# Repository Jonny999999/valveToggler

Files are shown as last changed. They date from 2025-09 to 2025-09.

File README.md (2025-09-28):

# ValveToggler-24V (Pneumatic Dust Filter Shaker)
Small analog controller PCB that drives a **5/3 pneumatic valve (2 coils)** to shake dust filters of a wood-chip extraction system (*Holzspäne-Absaugung*).  

<p align="center">
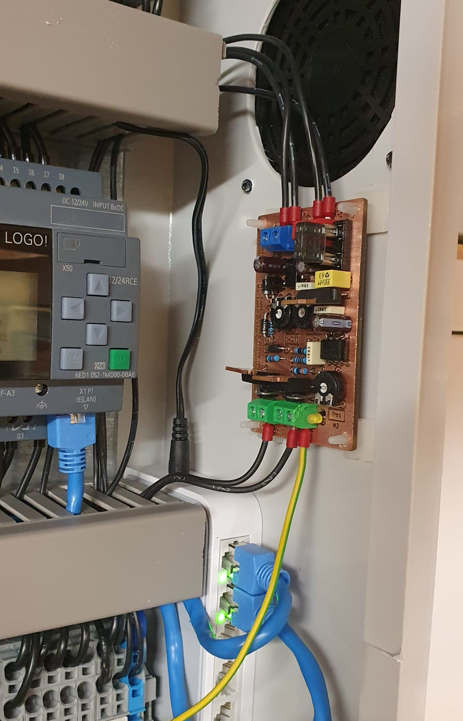
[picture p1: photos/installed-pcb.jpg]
Installed PCB – ValveToggler-24V
  
</p>

*Motivation:* Take switching stress off a LOGO! PLC's **relay outputs** (high-frequency switching, inductive load, continuous use over years) by moving the coil drive to **MOSFETs** and hardware timers. The PLC now only provides **high-impedance continuous signals** to enable/disable the shaking in the desired mode.

---

## System Hardware
- **24 V DC** supply (same rail as valve coils)
- **5/3-way pneumatic valve** with two **24 V** coils
- **Double acting pneumatic cylinder** shaking the filters
- **Mechanical stops** at cylinder's limits for abrupt stop so the dust falls off
- Two PLC control lines: `MODE_SINGLE_24V`, `MODE_DOUBLE_24V` (double has priority)

## PCB Features
- Steps **24 V** mode lines to **12 V**, generates timing with 2x **NE555**
- **Modes & timing**  
  - **SINGLE:** Toggle Coil1 only, with independent **ON/OFF** time (typ. ~300 ms ON, ~1.0 s OFF)  
     Adjustable range ≈ **70 – 400 ms** / **0.1 – 3 s**
  - **DOUBLE:** **50 % duty**, **complementary** coil drive (COIL1 = ¬COIL2)  
     Half-period adjustable from **50 ms to 3 s**
- **Low-side N-MOSFET** drivers, flyback/TVS, indicator LEDs
- Input priority & interlock to prevent both coils ON

---

## Files
- **[Schematic (PDF)](export/ValveToggler_schematic.pdf)**
- **[Layout (PNG)](export/ValveToggler_layout.jpg)**

## Schematic + layout preview:  
<p align="center">
  <a href="export/ValveToggler_schematic.pdf">
    Schematic
  </a>
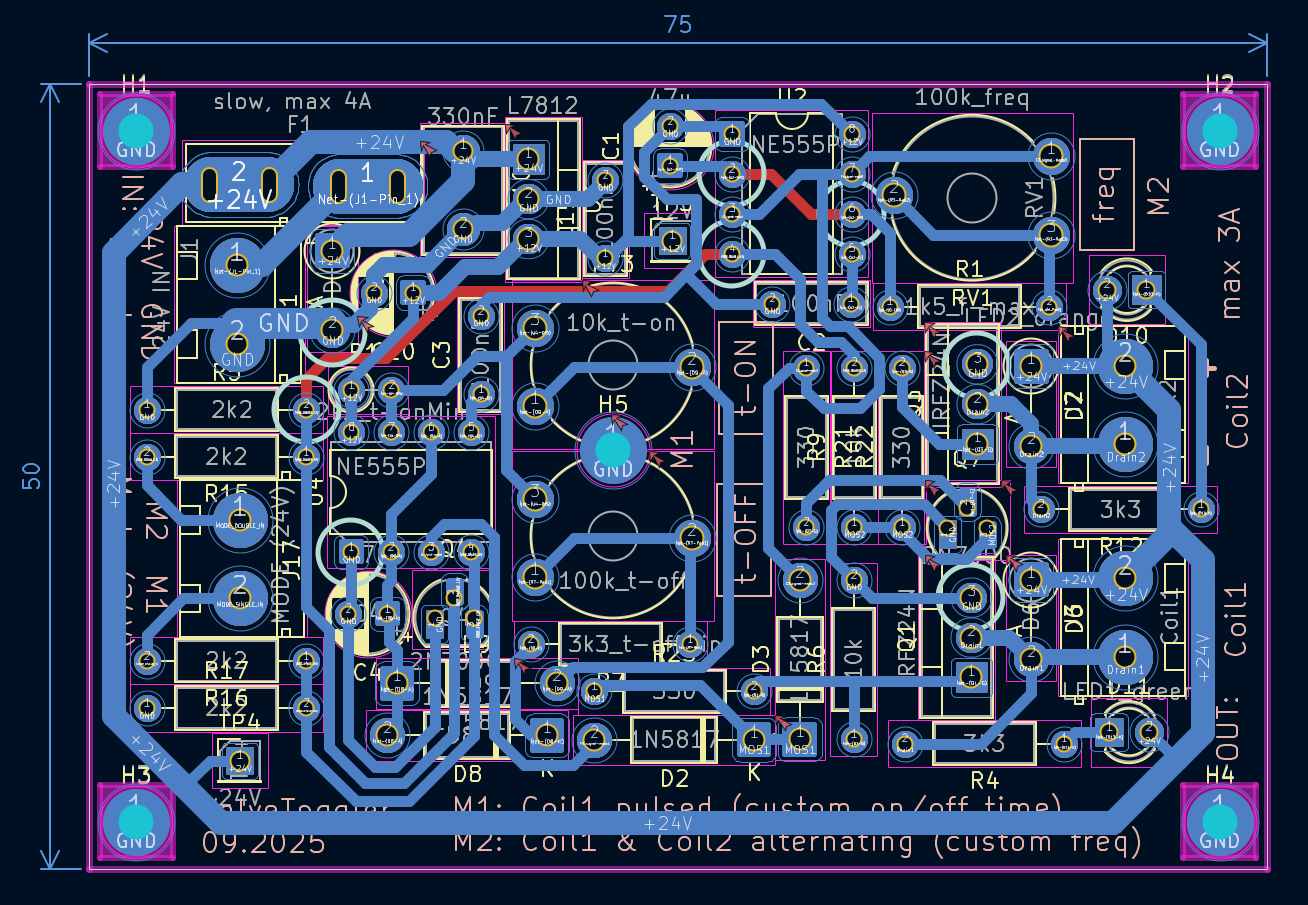
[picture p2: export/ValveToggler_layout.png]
PCB Layout
  
</p>

## Photos
Milling and Soldering:
<p align="center">
  <a>
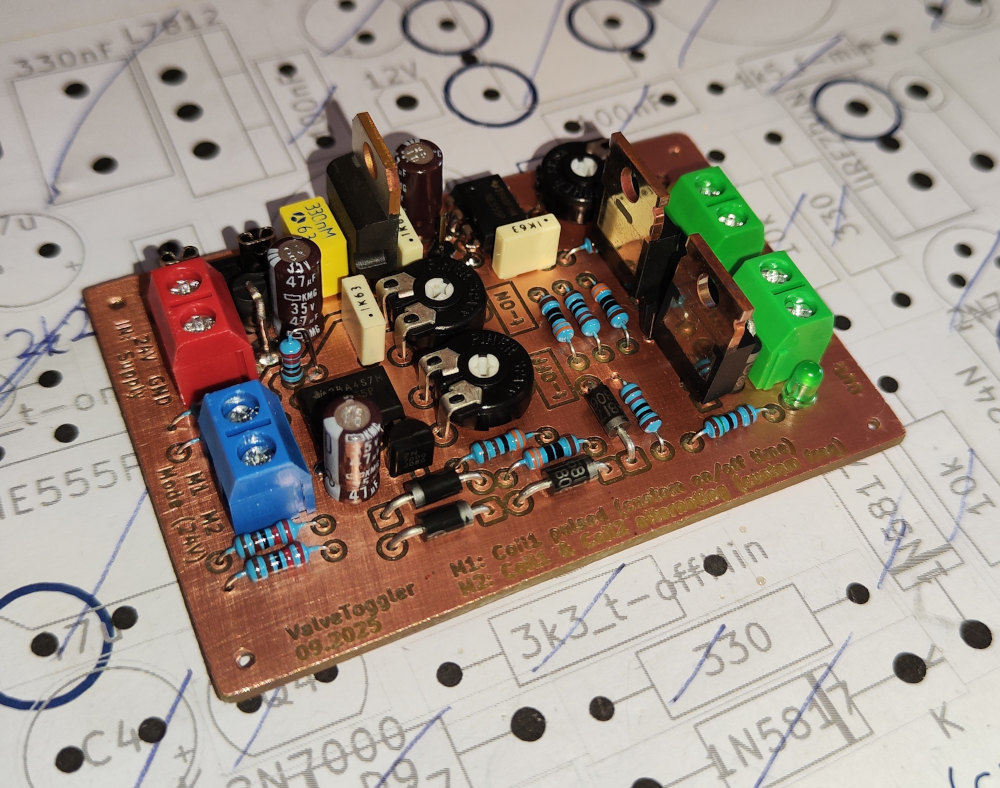
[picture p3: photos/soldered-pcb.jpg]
soldered pcb
    
  </a>
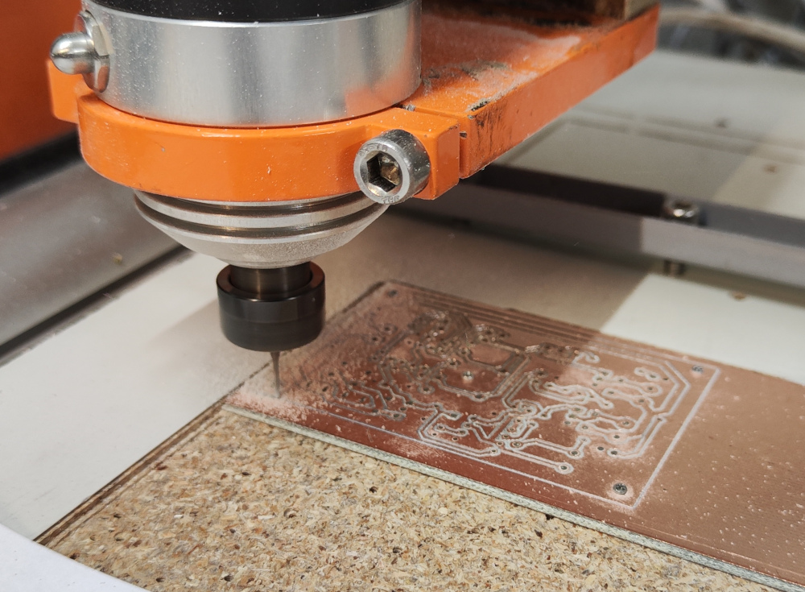
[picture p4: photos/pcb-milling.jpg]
pcb milling
    
</p>

<br>

3D-Model and Finished pcb:
<p align="center">
  <a>
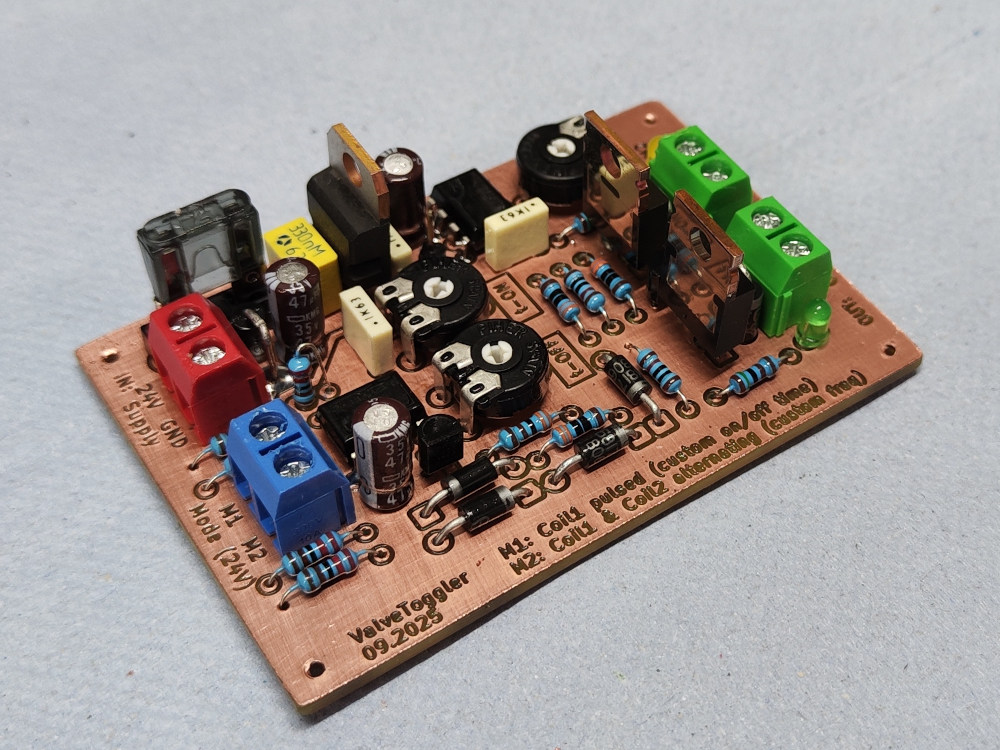
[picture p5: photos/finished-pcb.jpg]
    
  </a>
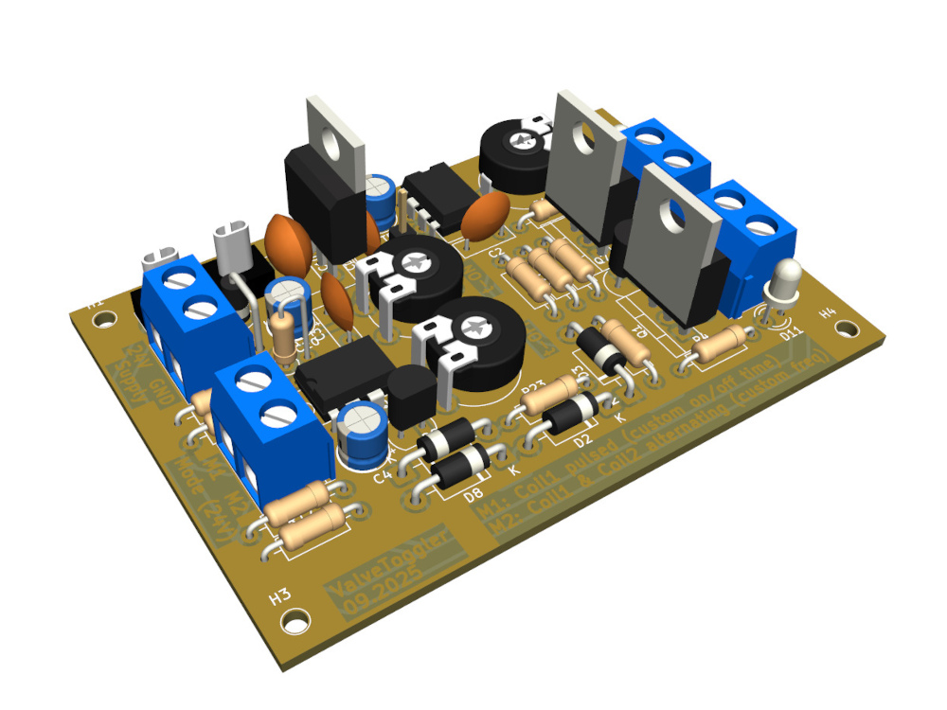
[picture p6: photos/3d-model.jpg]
3d model
    
</p>

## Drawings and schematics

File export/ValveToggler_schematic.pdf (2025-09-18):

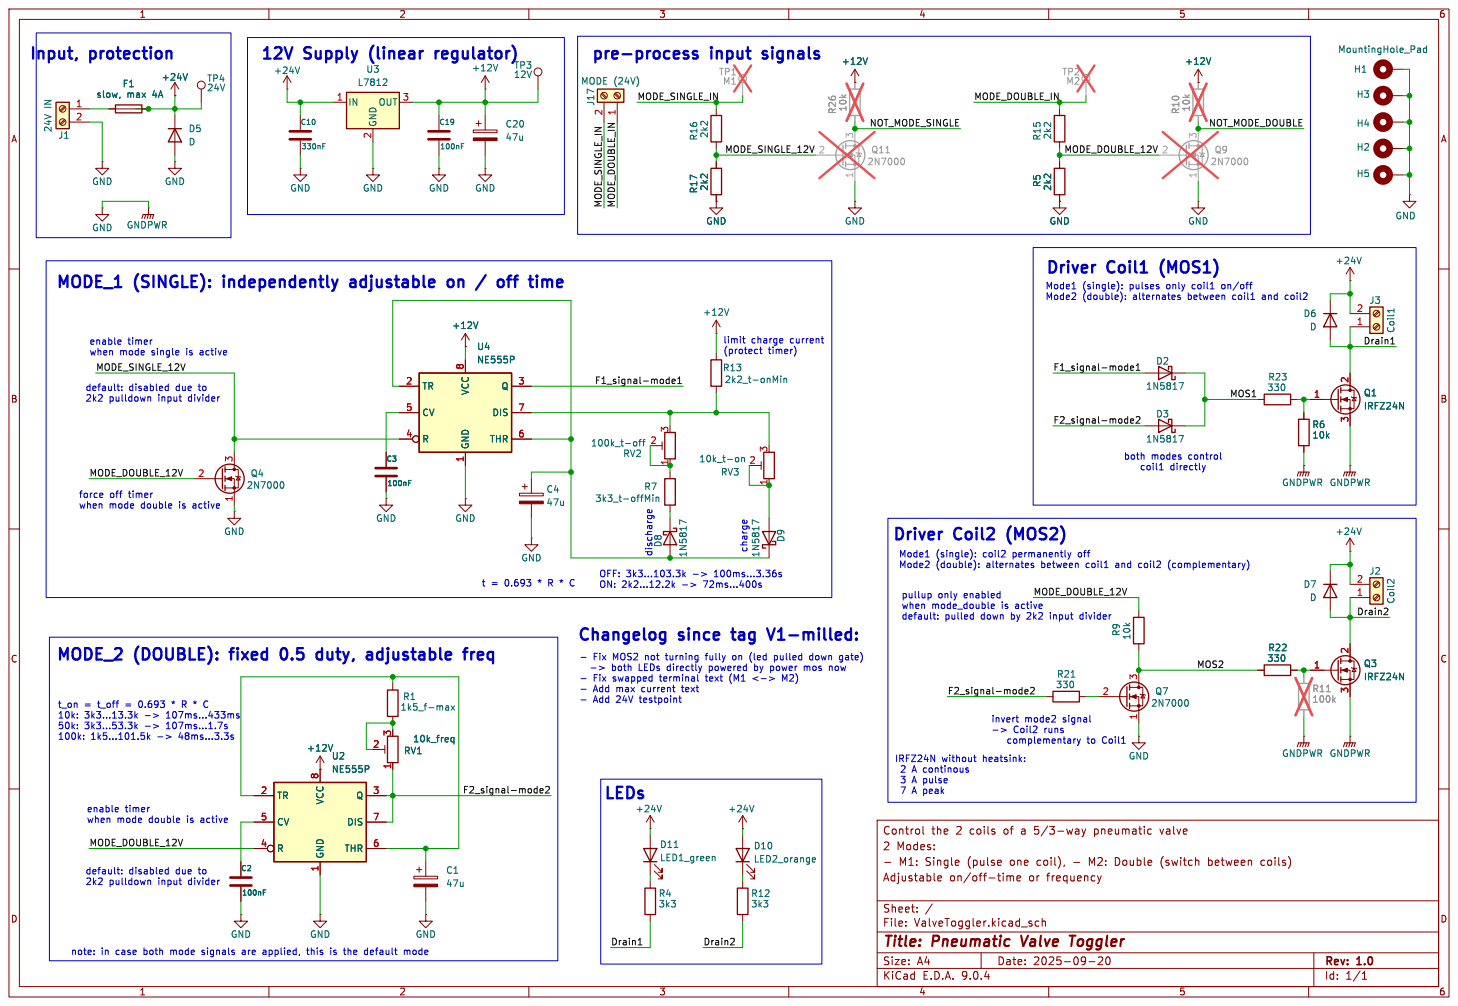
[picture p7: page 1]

both modes control coil1 directly

- Fix MOS2 not turning fully on (led pulled down gate)

- Add max current text - Add 24V testpoint D4
1k5_f-max +12V GND

IRFZ24N without heatsink: 2 A continous 3 A pulse

enable timer when mode double is active

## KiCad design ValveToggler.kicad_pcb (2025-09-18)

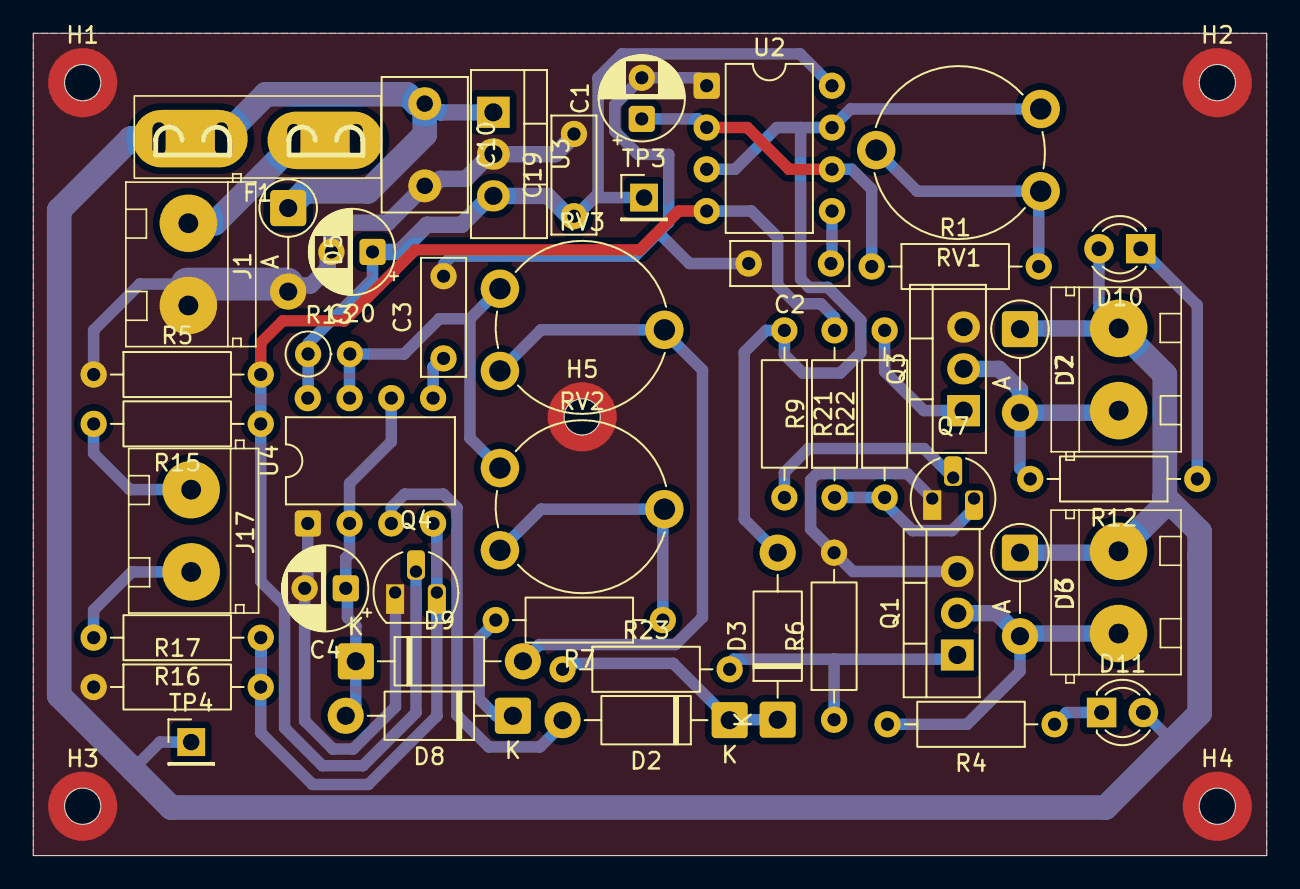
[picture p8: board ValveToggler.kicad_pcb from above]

Board: 4 copper layers, 75.0 x 50.0 mm, 52 parts (0 on the bottom side), 28 nets.

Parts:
C1, C4, C20: 47u; CP_Radial_D5.0mm_P2.50mm
C2, C3, C19: 100nF; C_Disc_D7.0mm_W2.5mm_P5.00mm
C10: 330nF; C_Disc_D8.0mm_W5.0mm_P5.00mm
D2, D3, D8, D9: 1N5817; D_DO-41_SOD81_P10.16mm_Horizontal
D5, D6, D7: D; D_DO-41_SOD81_P5.08mm_Vertical_AnodeUp
D10: LED2_orange; LED_D3.0mm_Clear
D11: LED1_green; LED_D3.0mm_Clear
F1: slow, max 4A; Fuseholder_Automotive-Mini_Fuse11x4x16_Footprint15x5_Inline
H1, H2, H3, H4, H5: MountingHole_Pad; MountingHole_2.2mm_NPTH-with-pad_DRC-clearance-error
J1: 24V IN; ScrewTerminal_P5mm_2Pin_FP10x8
J2: Coil2; ScrewTerminal_P5mm_2Pin_FP10x8
J3: Coil1; ScrewTerminal_P5mm_2Pin_FP10x8
J17: MODE (24V); ScrewTerminal_P5mm_2Pin_FP10x8
Q1, Q3: IRFZ24N; TO-220-3_Vertical
Q4, Q7: 2N7000; TO-92_HandSolder
R1: 1k5_f-max; R_Axial_DIN0207_L6.3mm_D2.5mm_P10.16mm_Horizontal
R4, R12: 3k3; R_Axial_DIN0207_L6.3mm_D2.5mm_P10.16mm_Horizontal
R5, R15, R16, R17: 2k2; R_Axial_DIN0207_L6.3mm_D2.5mm_P10.16mm_Horizontal
R6, R9: 10k; R_Axial_DIN0207_L6.3mm_D2.5mm_P10.16mm_Horizontal
R7: 3k3_t-offMin; R_Axial_DIN0207_L6.3mm_D2.5mm_P10.16mm_Horizontal
R13: 2k2_t-onMin; R_Axial_DIN0207_L6.3mm_D2.5mm_P2.54mm_Vertical
R21, R22, R23: 330; R_Axial_DIN0207_L6.3mm_D2.5mm_P10.16mm_Horizontal
RV1: 100k_freq; Potentiometer_Piher_PT-10-V10_Vertical
RV2: 100k_t-off; Potentiometer_Piher_PT-10-V10_Vertical
RV3: 10k_t-on; Potentiometer_Piher_PT-10-V10_Vertical
TP3: 12V; PinHeader_1x01_P2.54mm_Vertical
TP4: 24V; PinHeader_1x01_P2.54mm_Vertical
U2, U4: NE555P; DIP-8_W7.62mm
U3: L7812; TO-220-3_Vertical

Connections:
+12V: C19.1, C20.1, R13.1, TP3.1, U2.8 (VCC), U3.3 (OUT), U4.8 (VCC)
+24V: C10.1, D5.1 (K), D6.1 (K), D7.1 (K), D10.2 (A), D11.2 (A), F1.2, J2.2, J3.2, TP4.1, U3.1 (IN)
/Drain1: D6.2 (A), J3.1, Q1.2 (D), R4.2
/Drain2: D7.2 (A), J2.1, Q3.2 (D), R12.2
/F1_signal-mode1: D2.2 (A), U4.3 (Q)
/F2_signal-mode2: D3.2 (A), R21.1, RV1.1, U2.3 (Q), U2.7 (DIS)
/MODE_DOUBLE_12V: Q4.2 (G), R5.2, R9.2, R15.1, U2.4 (R)
/MODE_DOUBLE_IN: J17.1, R15.2
/MODE_SINGLE_12V: Q4.3 (D), R16.1, R17.2, U4.4 (R)
/MODE_SINGLE_IN: J17.2, R16.2
/MOS1: D2.1 (K), D3.1 (K), R23.1
/MOS2: Q7.3 (D), R9.1, R22.1
GND: C1.2, C2.2, C3.2, C4.2, C10.2, C19.2, C20.2, D5.2 (A), H1.1, H2.1, H3.1, H4.1, H5.1, J1.2, Q1.3 (S), Q3.3 (S), Q4.1 (S), Q7.1 (S), R5.1, R6.2, R17.1, U2.1 (GND), U3.2 (GND), U4.1 (GND)
unnamed: C4.1, D8.2 (A), D9.1 (K), U4.2 (TR), U4.6 (THR)
unnamed: D8.1 (K), R7.2
unnamed: D9.2 (A), RV3.1, RV3.2
unnamed: D10.1 (K), R12.1
unnamed: D11.1 (K), R4.1
unnamed: F1.1, J1.1
unnamed: Q1.1 (G), R6.1, R23.2
unnamed: Q3.1 (G), R22.2
unnamed: Q7.2 (G), R21.2
unnamed: R1.2, RV1.2, RV1.3
unnamed: R7.1, RV2.1, RV2.2
unnamed: C2.1, U2.5 (CV)
unnamed: C1.1, R1.1, U2.2 (TR), U2.6 (THR)
unnamed: C3.1, U4.5 (CV)
unnamed: R13.2, RV2.3, RV3.3, U4.7 (DIS)

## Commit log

2025-09-10 init - pcb schematic: timer tested, logic wip
    [ValveToggler.kicad_pcb, ValveToggler.kicad_sch]
2025-09-10 Rework logic (drop PNP, default on coil, pulldown-OR)
    [ValveToggler.kicad_sch]
2025-09-11 Optimize logic (more current, but significantly fewer parts)
    [ValveToggler.kicad_sch]
2025-09-11 Layout: Arrange footprints, start poc routing
    [ValveToggler.kicad_pcb]
2025-09-12 Routing complete, DRC pass
    [ValveToggler.kicad_pcb, ValveToggler.kicad_sch]
2025-09-14 Add R to trimmer (offMin), rework routing, Add timing calculation notes
    [ValveToggler.kicad_pcb, ValveToggler.kicad_sch]
2025-09-14 Add pcb2gcode script + config from gate repo (pcb_isolated-gate-control)
2025-09-15 Final adjustments pre milling: Mounthole, Text layer, Text thickness
    [ValveToggler.kicad_pcb, ValveToggler.kicad_sch]
2025-09-17 Arrange Fab text, Update actually soldered Values, Add milled gerber export
    [ValveToggler.kicad_pcb, ValveToggler.kicad_sch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]
2025-09-17 Add README, photos, schematic export
2025-09-18 Fix mos1 not turning fully on (rework leds), Fix swapped text, Add changelog
    [ValveToggler.kicad_pcb, ValveToggler.kicad_sch]
2025-09-18 Update exports (schematic, layouy, gerber), Add final photo
    [ValveToggler-B_Cu.gbr, ValveToggler-Edge_Cuts.gbr, ValveToggler-F_Cu.gbr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]
2025-09-28 Add photo of installed pcb
